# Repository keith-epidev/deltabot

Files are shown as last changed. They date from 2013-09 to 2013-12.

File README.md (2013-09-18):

Deltabot Project
================

This 'DeltaBot' is the product of Keith Brown's final year electronics project at [La Trobe University](http://www.latrobe.edu.au/). It falls under the umbrella project called [RepRap](http://reprap.org/). 

This repository serves as a place to store and track progress at a source level. Forcing software, hardware and designs into a single repository might not be the most practical use of git but it does allow me to easily share updates. Once the components come close to a stable release I will break this up into individual repos.

If you are interested, you can follow a brief blog at [http://printer.epidev.com](http://printer.epidev.com).

##Goals
- Cheap
- Modular
- CNC etching + 3D printing
- Produce alternative hardware, electonics and software. (Simply to learn)
- Automated Calibration

##Versions
There are three variants being produced by this project:  
1. Large robot  
2. Small, slow but strong platform  
3. Small, fast robot  

##Inspiration
Although I have not forked any current designs, this project is still based upon exiting work.
This project is primarily a derivative of the RepRap [Kossel](https://github.com/jcrocholl/kossel) by [jcrocholl](https://github.com/jcrocholl)
Of course I have also been inspired by other insane delta robots:
- [http://www.youtube.com/watch?v=Gv5B63HeF1E](http://www.youtube.com/watch?v=Gv5B63HeF1E)
- [http://www.youtube.com/watch?v=0-Kpv-ZOcKY](http://www.youtube.com/watch?v=0-Kpv-ZOcKY)
- [http://www.youtube.com/watch?v=NDzUiZsbQtw](http://www.youtube.com/watch?v=NDzUiZsbQtw)

And every other RepRap printer. But mostly The RepRap Project founder, Adrian Bowyer.
- [http://en.wikipedia.org/wiki/File:Adrian_Bowyer_-_PopTech_2007.webm](http://en.wikipedia.org/wiki/File:Adrian_Bowyer_-_PopTech_2007.webm)

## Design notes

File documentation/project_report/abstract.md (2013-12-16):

#(abstract.tex){
This document describes the design and development of an inexpensive 3D printer. The project is developed for the final year engineering project at La Trobe University by Keith Brown.

The printer will be in the form of a delta machine. The intention is to reduce the number of components and utilise cheaper hardware while still achieving a fast accurate print. The electronics will not be a direct derivative of current implementations. Experimentation with alternative architecture will be trialled with the goal of delivering a more computational capable system.

An introduction into 3D Printing and its concepts, advantages and issues is outlined. The commercial viability for both commercial and consumer markets is described. An analysis of both the structure and the systems inverse kinematic equations are included. Considerations regarding fluid motion is outlined. Hardware diagrams and descriptions follow. The electronic and software systems are discussed in detail. Testing procedures and associated results are also examined. Finally, project management tasks are reviewed.

}

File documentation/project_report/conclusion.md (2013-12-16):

Conclusion
==========

The macro and micro effects of an introduction to a personal manufacturing device is fascinating. It has the possibility to facilitate innovation in many areas. 
Whether it is a domestic or commercial application, 3D printing can help produce specialised parts, reduce prototyping time and cost, promote first hand recycling and entice the next generation into a technical field.

Low cost additive manufacturing is still in early development. A young underdeveloped device or idea presents an opportunity for improvement. This technology will continue to advance as demand increases. The delta style of 3D printers already is faster and more accurate then the traditional Cartesian machines.

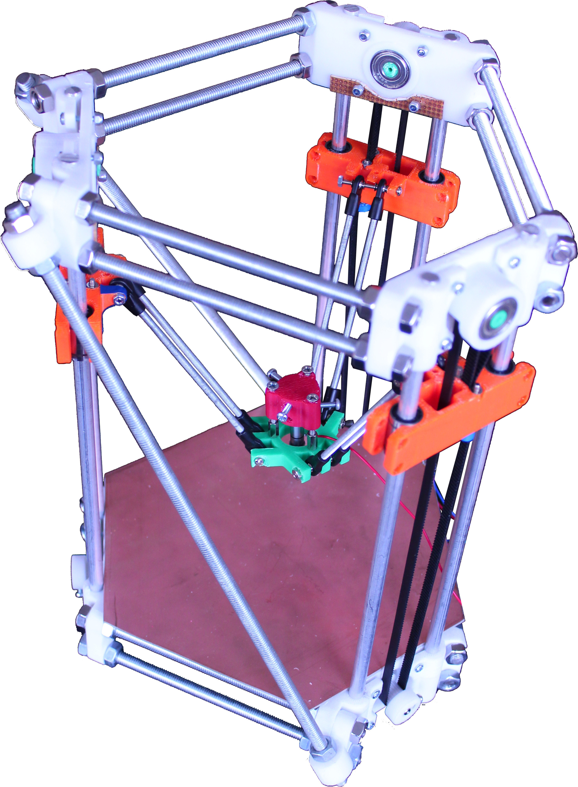
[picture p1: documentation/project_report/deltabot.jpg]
Final Deltabot Revision


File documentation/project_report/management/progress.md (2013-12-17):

Progress
========

A two complete frame has been designed and assembled. The first desktop model has a print area of roughly #10cm^3#. The second was a larger version using all the same printed parts but increasing the rod lengths. It is twice as tall and wide, resulting eight times the volume. This design has had small revisions made along the way and seems quite stable. The larger version does require a double cross strut for stability.

A plotter attachment was developed first for testing purposes. This has been used extensively. The extruder feed has also been prototyped although it has not been properly tested.

The second revision of electronics has been assembled and tested. While far better then the first revision, a third would add extra features and improve stability. No hardware mods are required for basic functionality.

The firmware has been developed during the entire development stage. Slowly improving and adding additional features. Currently it supports:
- Queuing of motion instructions
- Acceleration
- Console interface over UART
- LCD interface
- Homing and auto height calibration
- Command checksum validation

The complementary computer software is currently stable for 2D plots. It takes g-code generated from slic3r and converts it to motion descriptions for the printer. The communication side is capable of sending the instructions and validating that they were successfully received.

Shortcomings
-----------
For a complete working 3D printer the following tasks need to be completed:

- Develop extruder calculations for software
- Implement extruder feeder control
- Implement temperature PID loop
- Extend auto calibration
- Increase system clock to 20Mhz

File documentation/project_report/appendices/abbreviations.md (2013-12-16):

\chapter{Abbreviations}
\label{AppendixB}
\lhead{Appendix B. \emph{Abbreviations}}

| *ABS*  | *A*crylonitrile *b*utadiene *s*tyrene (plastic)                     |
| *AVR*  | *A*tmel's Alf (Egil Bogen) and *V*egard (Wollan)'s *R*ISC processor |
| *CAD*  | *C*omputer-*a*ided *d*esign                                         |
| *CPU*  | *C*entral *P*rocessing *U*nit                                       |
| *CRC*  | *C*yclic *R*edundancy *C*heck                                       |
| *FPU*  | *F*loating *P*oint *U*nit                                           |
| *MSP*  | *M*ixed *S*ignal *P*rocessor                                        |
| *LCD*  | *L*iquid *C*rystal *D*isplay                                        |
| *PLA*  | *P*oly*l*actic *a*cid (plasic)                                      |
| *SPI*  | *S*erial *P*eripheral *I*nterface                                   |
| *SVG*  | *S*calable *V*ector *G*raphics                                      |
| *UART* | *U*niversal *A*synchronous *R*eciever/*T*ransmitter                 |
| *USB*  | *U*niversal *S*erial *B*us                                          |
	List of abbreviations

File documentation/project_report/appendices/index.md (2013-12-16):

#(appendices.tex){

![documentation.md]
![abbreviations.md]
![schematics]
![layout]
![code.md]
![cad.md]

}

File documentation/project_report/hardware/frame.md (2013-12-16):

Frame
=====

The first iteration of design utilised aluminium to build the framework. It was selected due its strength and the modularity it offered during the prototyping stage.

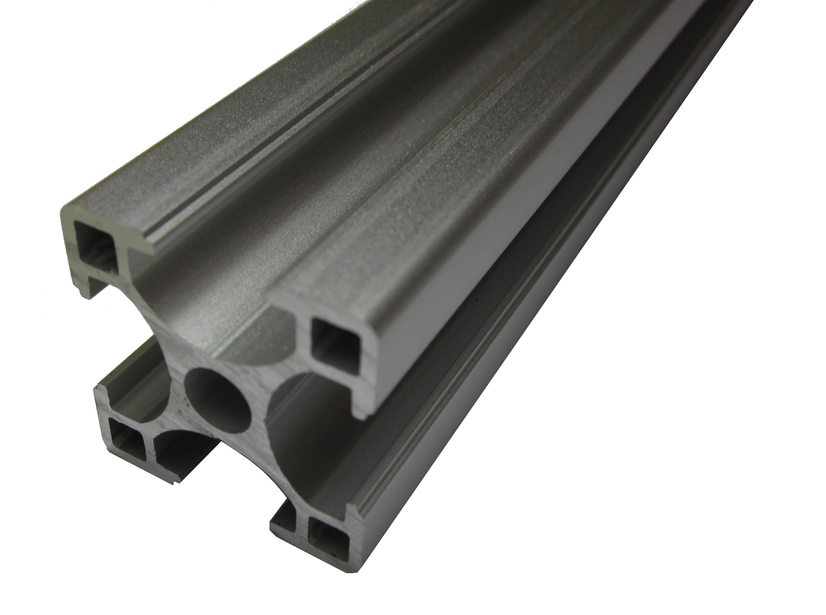
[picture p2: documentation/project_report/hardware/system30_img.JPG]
System30 Beam


Positives
- Very strong in any direction
- Simple mounting and joining
- Reusable
- Easy to modify / tune

Negatives
- Relatively expensive at $25 per meter
- Requires special cutting tools
- Hard to source

However during the initial design, it was decided that the carriage designs would be too complex which would violate one of our design goals. The very cheap and easily obtained 8mm threaded and smooth rods were used instead. This way we can use LM8UU linear bearings instead of investing a lot of time in hardware design.

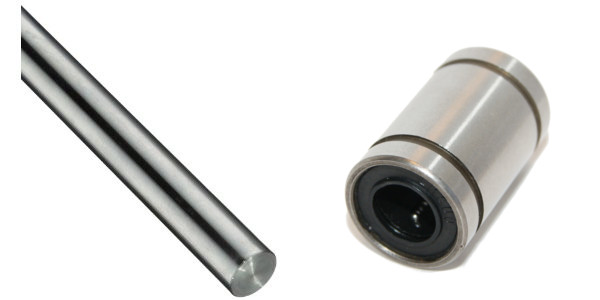
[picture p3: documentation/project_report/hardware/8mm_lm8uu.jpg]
8mm round bar and LM8UU Linear bearings

Positives
- $3.3 per meter for stainless steel round bar
- $0.90 per meter for 8mm threaded rod.
- $0.75 per unit for LM8UU linear bearings.
- Easy to obtain from metal fabricators or general hardware stores
- Can cut with a hacksaw or angle grinder

Negatives
- Flexes in the horizontal direction

Early Sktech Of Frame Design

The frame will have a small enclosed area for the electronics and power supply. The printer bed is mounted on top of the case. There is a beam on the top level that intersects the face in half. This is primarily for a place to mount the plastic feeder but also serves as a structural support beam.

We will need to know how much material to order. There is 4 equilateral triangles with side lengths of #D#  and there are 4 rails that need to be of #D#. 
##M_{threaded} = 3(4D) + 2(D\sqrt{3}) ##
##M_{smooth} = 3(2*2D)  ##
To minimise waste, #D# needs to be a multiple of the purchased material's length.  To further reduce waste, the purchased length should be close to a whole number.

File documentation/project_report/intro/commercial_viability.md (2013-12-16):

Commercial Viability
====================

This old technology is becoming established in a new market. While it becomes more accessible, new opportunities begin to emerge and intern, increases demand. Prices are decreasing, materials are becoming more accessible and there is an increasing amount of printable designs being uploaded to the Internet. The later attributes the most positive influence to the 3D printing market. This makes an old product more valuable.

Growth of CAD designs on thingiverse.com cite[6]

It is clear that this market is expanding at a promising rate. Furthermore because there is such a diverse range of neighbouring markets that will benefit from this technology, it is likely that it will be supported by commercial demand alone. Applications for 3D printing have yet to be completely discovered, the boundaries are always being pushed by innovators. It is apparent that a very successful industry has been created.

Commercial Market
-----------------

3D printing can help many different businesses. For example; Product designers can produce prototypes within a few hours, prosthetics can be made for a person more frequently and engineers can produce custom parts easily. It is important to note that even if a 3D printer existed in every home, there are still many skills that can't be replaced by automation. Downloading a generalised product will never replace a professionally crafted custom version. 3D printing just streamlines the development cycle and promotes rapid growth.

Rapid prototyping reduces development costs and creates new opportunities. It is possible that we will see a rise in hardware start-ups similar to the influx of software start-ups we have seen recently. It may be more feasible for a young company to attempt entering into established markets with little overhead.

Consumer Market
---------------

There is a number of reasons why an individual might desire a 3D printer. It may help reduce our consumption rate by allowing us to easily repair broken household items. While it is unlikely for the average person to need a miniature factory, it is ideal for hackers, hobbyists, artists and craftsmen

Currently, the largest consumer market for 3D printing falls inside the open source community. Although intellectual property is freely shared, support and labour is very valuable. These customers are generally open to early adoption of new technology. The network of passionate, diversely skilled customers strive to improve the current designs and collaboratively innovate the CNC scene.

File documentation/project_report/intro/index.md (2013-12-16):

Introduction
============

3D Printers have received a lot of media attention recently. Additive manufacturing has been around for at least 30 years cite[1, 2]. However, in the last five years popularity has increased dramatically due to the availability of much cheaper entry level machines. It is now possible for the general public to purchase pre-assembled printers at a similar cost as a personal computer.

There will always be innovation and dangers associated with a new technology. We already have prime examples of both aspects; At a 2011 TED talk, Dr Anthony Atala presented a human kidney prototype that his team had printed cite[3]. Late 2012 Cody Wilson uploaded a video to Youtube that showed himself firing a gun mostly composed of 3D printed parts cite[4].

The environment will benefit from this new way of producing products. Firstly, plastic items can be recycled and reused to create new, more useful items. This not only reduces costs but it also eliminates transportation of new items. They no longer need to be imported and transported all over the country, they can just be downloaded.

Whilst companies like Objet and Stratasys produce printers for the commercial sector, it is hobbyist style printers that have spread awareness of such technology. The Reprap foundation has produced numerous models under the GPL licence. Their main goal is to produce an affordable device that can self replicate. All of the designs are available to download and print. Makerbot Industries is a comercial operation that was born from an open source community.

Online services such as Shapeways provides 3D printing services. This allows their customers to receive a higher quality print without investing in expensive hardware. CAD design community sites have also been very popular such as 'thingiverse.com'. There are over 30,000 free designs including a key-chain fob, mobile phone case, model radial engine and even 3D printer parts and upgrades.

![printing_methods.md]
![fdm_articulation_implementations.md]
![fdm_accuracy_materials.md]
![proposed_solution.md]
![commercial_viability.md]

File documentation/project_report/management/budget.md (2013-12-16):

Budget
======

There are many consumer 3D printers on the market currently. They range from $450 to over $20,000. One of the primary goals of this project is to produce inexpensive electronics to help reduce the overall cost of 3D printing. $450 is very competitive if the quality is reasonable. The final target cost for this project is a base model for $350 AUD. I have considered many aspects that will help minimise costs:

- low end 8bit AVR ATmega value line microcontrollers
- Single board solution
- Optional components: Flash memory, LCD and Ethernet.
- Minimal hardware
- Printed gears for belt drive
- Balance of cost vs quality for stepper motors
- Use common hardware store smooth and threaded rods

Revenue
-------
La Trobe University kindly provides a $200 spending budget for final year projects. I will personally fund the remaining fees.

Expenses
--------
Most parts were able to be recycled through each design iteration.

| Item                     | Cost |
|──────────────────────────|──────|
|──────────────────────────|──────|
| 6 meters of smooth rod   | $20  |
| 6 meters of threaded rod | $6   |
| PCB Fabrication          | $40  |
| Electronic components    | $70  |
| 4 Stepper motors         | $60  |
| 1kg ABS Plastic          | $30  |
| Assembled Extruder       | $50  |
| Power supply             | $30  |
| Heated Bed               | $50  |
| 4 metes of Belts         | $16  |
| 6 608zz Bearings         | $6   |
| 6 LM8UU Bearings         | $8   |
| Assorted hardware        | $50  |
|──────────────────────────|──────|
| Total                    | $436 |
|──────────────────────────|──────|
	Budget allocation

Non-budgeted resources
----------------------

| Item                                                                       | Provided By                           |
|────────────────────────────────────────────────────────────────────────────|───────────────────────────────────────|
|────────────────────────────────────────────────────────────────────────────|───────────────────────────────────────|
| Atmel AVR Dragon JTAG programmer                                           | Robert Ross                           |
| Host computer and development software                                     | Keith Brown                           |
| Soldering equipment                                                        | Department of Electronics Engineering |
| CRO and testing equipment                                                  | Department of Electronics Engineering |
| Breadboard, Pliers, cutters, Multimeter and other general electronic items | Keith Brown                           |
|────────────────────────────────────────────────────────────────────────────|───────────────────────────────────────|
	Non-budgeted resources

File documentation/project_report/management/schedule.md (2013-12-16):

Schedule
========

The original schedule had to be modified in order to accommodate the extra unplanned revisions for both hardware and electronics. From May up until late October, three design iterations of hardware were developed. Each time improving on a major design flaw. Each iteration had a large impact on the schedule, however all were necessary hurdles that contributed to the final product. A second revision of electronics was required after the project goals were re-evaluated and to remove a few bugs.

The additional time added to the timeline pushed some of the key functionality past important dates such as the final presentation. Work has continued after the main delivery dates and a fully functioning 3D printer is estimated to be achieved at the end of January 2014.

An online project log was kept. Posts were made at regular intervals, discussing progress and small milestones. This served as a great resource and helped keep track of ongoing progress. It is available at [http://printer.epidev.com](http://printer.epidev.com).

![gantt.tex]

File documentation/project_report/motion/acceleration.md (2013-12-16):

Acceleration
============

Acceleration is required to ensure smooth motion is maintained. Smooth motion is essential for reaching high speeds and also to minimise a stepper motor skipping a step. The rate of acceleration can be written as a function of current and next frames momentum.  We are only concerned with the momentum of the actuator carriages, not the momentum of the platform.

## P = mv ##
where #P# is momentum,
#m# is mass,
#v# is velocity.
So to decrease momentum around sharp bends, we must reduce the speed of the actuator.

Once the system has been constructed, we will need to run tests to work out the maximum speed that we should attempt to accelerate to. Jerk is the derivative of acceleration. It can be thought of as how fast can we accelerate? This also will need to be thoroughly tested. But we can write it as a variable so that we can later substitute different values.

The acceleration algorithm is as follows:

- calculate the closest change in direction for any actuator
- if change is less then 100 steps decrease speed by A
- if change is greater then 100 increase speed by A
- if maximum speed has been reached do nothing.
- repeat next step

This creates a smooth linear acceleration. We could also implement more detailed patterns that perhaps use a quadratic to reach the maximum speed sooner.

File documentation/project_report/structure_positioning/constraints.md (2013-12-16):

Constraints
===========

Printing Bed
------------
A design assumption was made at the beginning of this section; The platform can not be positioned outside of the frame. To force this rule to apply, we must set the linkages length equal to the minimum distance from a rail to a side of the frame. The maximum length required is a line straight down the y axis from the rail to the frame which is equal to #{\sqrt{3}\over 2}D#. If we swing the platform around, pushing it to the maximum radius that this length permits, we see that the path is not actually a circle but a rounded triangle. The light blue path in fig. ref[top-view-angle_diagram.svg] is the maximum positions. Such an unusual path is typically not needed, so we will simplify our problem by using a circular print bed.

To allow for a platform, we must subtract its radius from each of the linkages length. So, our rule for #h# is:
##h = {\sqrt{3}\over 2}D - r ##

Universal Joint Angle Range
---------------------------

Universal joint angle horizontal range

The universal joints that will pivot to allow full movement will need to be capable of a certain range. This can be calculated exactly with:

## \theta = 60 - 2 \arctan{({  { {2 - \sqrt 3 }\over 2} r  \over  {1\over 2} D   } )} ##

Practically, we can simplify the problem by aiming for #60^{\circ}# in the horizontal direction and #90^{\circ}# in the vertical direction.

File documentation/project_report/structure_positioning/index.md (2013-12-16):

Structure and Inverse Kinematics 
================================

The hardware design will be in the form of a delta machine. These devices can perform fast accurate tasks as the light-weight print head is capable of quick acceleration. This design has been adopted from a current reprap project cite[5]. The delta machine will use less parts then a traditional Cartesian machine.

For a detailed overview of this projects design please refer to the Design Document

![structure.md]
![one_dimension.md]
![platform.md]
![vertical_travel.md]
![two_dimension_vert.md]
![two_dimension_horz.md]
![platform_horz.md]
![three_dimension.md]
![constraints.md]

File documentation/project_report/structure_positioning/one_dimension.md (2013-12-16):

Simple one dimension position
===========================

Lets consider one dimension to begin with, Figure 1 illustrates the movement of three key points; the platform and the left and right linear actuators. We can see that if the linkages are the same length as the vertical distance, the platform is capable of reaching any position along the #x# axis.

//[Simple ideal motion](svg:1)

Also, it can be seen that a vertical actuator requires an equal amount of travel to permit full movement. It is important to note that the platform is considered a point source in this example. Practically this is not the case as we will require a place to mount tools.

For a desired position of #p(x)#, we need to derive where to place linear actuators. Take fig. ref[structure_simple.svg] below, lets derive the equations that will translate a desired #x# into #a_1# and #a_2#. 

Simple one dimension parameters

Firstly, lets derive relationship between #x# and #a_1#:
## (1)\  h^2 = a^{2}_{1} + b^{2}_{1} ##
##  \Leftrightarrow  a_{1} = \sqrt{ h^2 - b^{2}_{1} }##
## (2)\  b_1 = x - (-D)##
## \Leftrightarrow\  b_1 = x + D##
substituting (1) into (2) gives
## a_1(x) = \sqrt{ h^2 - ( x + D )^2 }##
Now, lets find the relationship between #x# and #a_2#:
## (3)\  h^2 = a^{2}_{2} + b^{2}_{2}##
##  \Leftrightarrow  a_{2} = \sqrt{ h^2 - b^{2}_{2} }##
## (4)\  b_2 = x - D##
finally, substituting (4) into (3)
## a_2(x) = \sqrt{ h^2 - (x - D)^2 } ##

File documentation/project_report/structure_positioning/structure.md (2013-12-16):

Structure
=========

A delta machine consists of a number of kinetic chains that meet at a central platform. This platform can be moved by actuating the pivots connected to the main structure. The platform is kept parallel to the floor during motion. Figure ref[structure_diagram.svg] represents a simple two armed delta machine. The two-dimensional diagram helps to illustrate the important lengths and vectors. After we have analysed a two dimensional machine we will apply these concepts to three-dimensions.

Structure Diagram

| #D# | Distance from actuator to origin                       |
| #L# | Vertical length of the frame                           |
| #a# | Height of the actuator pivot point from the origin     |
| #h# | Length of the kinetic linkage                          |
| #r# | Radius of the platform                                 |
| #p# | Position of the extruder tip or centre of the platform |
| #O# | Origin of the system                                   |
| #x# | Horizontal vector                                      |
| #y# | Vertical vector                                        |
| #z# | Depth vector                                           |
|─────|────────────────────────────────────────────────────────|
	List of vectors

The following assumptions are made to help define the system:
- Platform and linkages must stay within the frame's outer rails.
- Linkages are not restricted in any way, they may swivel on their joins in any direction.
- The platform can not move down past the base.
- Linkages are restricted to the rail's length.
- Linkages can not stretch or contract.

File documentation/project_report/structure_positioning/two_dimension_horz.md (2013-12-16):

Two dimensional position in the horizontal plane
==============================================

Now its time to examine how adding a third actuator allows for two dimensional movement in the horizontal plane. Figure ref[top-view_diagram.svg] is a top-down view of our system. The actuators are placed in a equilateral triangle formation to distribute the load evenly. The position of the platform can be altered by changing the lengths of the linkages horizontal component, the #b# term. Remember, this is not stretching the linkages, it is merely displacing length between the horizontal and vertical component - the hypotenuse remains the same. By looking straight down into the system, only the #b# vectors are visible, the carriages on the rails or the #a# term is  directed in/out of the page.

The coordinates system has been aligned with the actuators to help simplify the problem. The origin is placed at the centre of the print bed. Please note that the print bed is represented as a circle with its radius equal to the minimum distance from the origin to the frame. 

To control the platforms position we must modify the carriages vertical position #a#. However, the horizontal plane position is completely dependent on #b#. We have already established the relationship between #a# and #b#, and that is #a = \sqrt{ h^2 - b^2}#. We now need to develop the relationship between #b# and the position (#x,y)#.

Each actuator will have its own equation for calculating its #b# term. This is because they are not placed uniformly around the coordinates system even though they are equally apart. Firstly, the general rule for calculating #b# as a function of the platforms position:
##b_n(x,y) = |\overrightarrow{R_n P(x,y)}|## Where R is the position vector of the target actuator and P is the position vector of the platform.

Top view components

Figure ref[top-view_diagram.svg] illustrates that this problem can be solved by a simple application of Pythagoras' theorem again.

Top actuator:
##d_1(x) =  x##
##e_1(y) =  y - D##
##b_1(x,y) = \sqrt{d_1^2 + e_1^2}##
##b_1(x,y) = \sqrt{ x^2 + (y - D )^2}##
Bottom left actuator:
##d_2(x) = x - (-d\sqrt{3}/2)##
##e_2(y) = y - (-d/2)##
##b_2(x,y) = \sqrt{ ( x + {d\sqrt(3)\over 2})^2 + ( y + {d\over 2})^2   } ##
Bottom right actuator:
##d_3(x) = x - D\sqrt{3}/2##
##e_3(y) = y - (-D/2)##
##b_3(x,y) = \sqrt{ ( x - {D\sqrt(3)\over 2})^2 + ( y + {D\over 2})^2   } ##

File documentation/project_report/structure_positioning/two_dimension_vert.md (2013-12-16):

Two dimensional position in the vertical plane
============================================

Now we are able to examine how we may add a vertical component to the system. From the last sections we discovered that the length required for the vertical actuators is the equal the linkages length. In this example, we have created a square printable area of #(2D)^2#. This is possible as the rails are twice the length of the linkages length or #L = 2(2D)#. 

//[Two dimensional motion](svg.4)

Introducing the #z# component directly adds to the #a_1# and #a_2# terms. The position equations are amended as:

## a_1(x) = \sqrt{ h^2 - (x + D - r)^2 } \color{red}{ + z}##
## a_2(x) = \sqrt{ h^2 - (x - D + r)^2 } \color{red}{ + z}##

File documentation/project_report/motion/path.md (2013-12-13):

Path Tracing
============

Once a three dimensional object has been split up into two dimensional layers, the extruder head must trace the outlines of each layer. Once a layer has been traced, the z component moves a step down and the extruder will trace the next layer. The process repeats until all layers have been extruded leaving a fully formed three dimensional object.

To move the extruder in a desired direction, we must calculate the distance and direction that each actuator must travel. This can be done by subtracting actuator heights from the last position with the heights of the next move. This gives us three vectors describing the distance and direction. The next step is to translate these distances into corresponding speeds. To move in a straight line, each actuator must complete their respective distances at the same time. 

So to calculate how fast each actuator must move, we first start with:

## speed = displacement / \Delta time ##

So we can see that keeping the time constant for all three actuators, only displacement affects speed. Actually speed is directly proportional to the distance that needs to be travelled. 

But how long is an acceptable time to travel? This is quite simple once the maximum speed is determined. The actuator with the largest displacement should travel at maximum speed.

## \Delta time = displacement / MAX(speed) ##

Now we simply substitute the same #\Delta time# for the other actuators. Now we have proportional motion!

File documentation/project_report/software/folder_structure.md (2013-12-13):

Folder Structure 
================

I have chosen to set the firmware directory in a way that attempt to separate non similar objects. For example system settings should not be located in the same directory as code for a LCD.

The following list illustrates the basic structure:

- *dev* contains sub folders that have code relating to physical components such as LCD and stepper motors
- *etc* contains configuration files such as clock speed, pin descriptions and macros
- *lib* contains reusable software objects such as buffers
- *main* holds different top level files (useful for different applications or tests)
- *sys* has anything to do with the microcontroller architecture

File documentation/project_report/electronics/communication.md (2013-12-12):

Communication
=============

An FTDI FT220X USB to UART converter is used for communication between the host computer and the printer. It runs at a baud rate of 38400, however burst commands can be sent due the internal FILO buffer included in the integrated circuit. A micro USB header was selected so that common android phone cables can be used.

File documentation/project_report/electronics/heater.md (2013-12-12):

Heating elements
================

A powerful MOSFET is used to push large current through a small resistor. This produces heat. The heat can be monitored with a robust thermistor. A PID loop will smoothly and accurately maintain a specific temperature. Two heat ports are available; one for the extruder and one a heated bed.

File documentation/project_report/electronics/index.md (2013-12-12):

Electronic Systems
==================

![methodology.md]
![top_level.md]
![microcontroller.md]
![motor_drivers.md]
![communication.md]
![heater.md]
![sensors.md]
![power.md]
![safety.md]

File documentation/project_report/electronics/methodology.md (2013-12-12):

Methodology
==========

The first iteration of electronics were designed around the goal of modularity. While it offered the needed flexibility during the prototyping stage, a few shortcomings forced a redesign. It featured small daughter boards that vertically plugged into a mainboard. Exposing a SPI bus as ports that could accept any type of add on provides a possible upgrade path in the event of a necessary addition. 

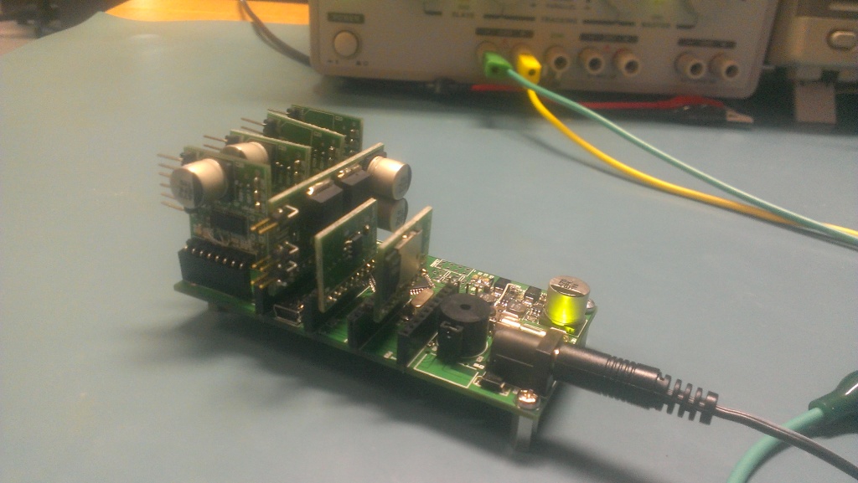
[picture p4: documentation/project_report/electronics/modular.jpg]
First iteration of electronics


Unfortunately this configuration was too flimsy. Stepper drivers were damaged during testing. There is a lot of manual work required to assemble such a design and would not be practical for a final product.

The second revision was designed to be a simple low-cost single board solution. Instead of being a complete standalone product, this version is designed to leverage of a host computer. No external memory is used so a computer must constantly feed G-Code commands during a print. 

Second revision

One of the main goals of revision two was to be cross compatible with the exiting community firmware. The most compatible firmware is ['Teacup'](http://github.com/Traumflug/Teacup_Firmware) . Furthermore, any software that I develop should be cross compatible with existing hardware such as RAMPS.

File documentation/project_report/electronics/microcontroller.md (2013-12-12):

Microcontroller
===============

The Microcontroller that has been selected is an Atmel 8-bit ATmega644. It was selected due to its low cost, small footprint and compatibility with existing firmware. The large ATmega family also allows for an upgrade path if required. It can be clocked up to 20MHz however I am using 10AU model which has a maximum of 10Mhz. The 10AU is available in single quantities at $4 compared to the 20Mhz at $11.

The package includes 64 Kbytes of flash memory. It has 44 pins with a total of 32 GPIO available. No USB communication is integrated so a USB to UART chip is required. The physical package selected was a TQFP so that it can be easily soldered with a standard soldering iron.

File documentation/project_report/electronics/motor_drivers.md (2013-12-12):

Motor Drivers
=============

TI DRV8825 integrated motor drivers were selected to drive the stepper motors. They can be configured to drive a single bipolar stepper motor at 2.5A with up to 1/32 microstepping. They do not require many external passive components. They feature a useful error signal pin that goes high in the event of over current or heating issues. A heat sink should provide adequate heat dissipation.

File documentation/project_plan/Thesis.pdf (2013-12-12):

LA TROBE UNIVERSITY (http://www.latrobe.edu.au)

# Delta Printer Project Plan

by

## Keith Brown

Final Year Project Report

in the
Faculty of Science, Technology and Engineering (http://www.latrobe.edu.au/scitecheng/) Department of Electronic Engineering (http://www.latrobe.edu.au/ee)

## December 2013

# Declaration of Authorship

La Trobe University | Department of Electronic Engineering

## Statement of Authorship INDIVIDUAL SUBMISSION

Please read the following instructions and associated University documents before completing and submitting this form with your item of assessment.
1. A Statement of Authorship must be completed for all items of assessment where the assessment is worth ten percent (10%) or more of the total for the unit.
2. The Academic Misconduct Policy found at http://www.latrobe.edu.au/policies
3. Statute 16 found at http://www.latrobe.edu.au/legalservices/statutes.html
4. Regulation 16.2 found at http://www.latrobe.edu.au/legalservices/regulations.html

I certify that the attached material is my original work. I declare that no other person's work has been used without due acknowledgement. Except where I have clearly stated that I have used some of this material elsewhere, it has not been presented by me for examination in any other course or unit at this or any other institution.
I have read the Academic Misconduct Policy, Statute 16 and Regulation 16.2 relating to Student Discipline and Academic Misconduct, which are available on the University's web site and understand that I am bound by such Policy, Statute and Regulation and that I may be subject to student discipline processes in the event of an act of plagiarism by me.
I understand the nature of plagiarism to include the reproduction of someone else's words, ideas or findings and presenting them as my own without proper acknowledgement. Further, I understand that there are many forms of plagiarism which include direct copying or paraphrasing from someone else's published work (either electronic or hard copy) without acknowledging the source; using facts, information and ideas derived from a source without acknowledgement; producing assignments (required to be independent) in collaboration with and/or using the work of other people; and assisting another person to commit an act of plagiarism.
I understand that the work submitted may be reproduced and/or communicated by the University or a third party authorised by the University for the purpose of detecting plagiarism.
I agree for the Department to keep a copy of my assignment for a database.
Unit Code: |
Unit Name: |
Lecturer/Tutor's name : |
Name of Document: |
Student Number: |
Family Name: |
Given Names: |
Signature of Student: |
Date Submitted: |

i

LA TROBE UNIVERSITY (http://www.latrobe.edu.au)

# Abstract

Faculty of Science, Technology and Engineering (http://www.latrobe.edu.au/scitecheng/)

Department of Electronic Engineering (http://www.latrobe.edu.au/ee)

Bachelor of Electronic Engineering

by Keith Brown

This document describes the project plan for an inexpensive 3D printer. The project is

developed for the final year engineering project at La Trobe University by Keith Brown.

The printer will be in the form of a delta machine. The intention is to reduce the number

of components and utilise cheaper hardware while still achieving a fast accurate print.

The electronics will not be a direct derivative of current implementations. Experimen-

tation with alternative architecture will be trialled with the goal of delivering a more

computational capable system.

An introduction into 3D Printing and its concepts, advantages and issues is outlined.

The commercial viability for both commercial and consumer markets is described. This

projects primary, secondary and tertiary objectives are listed. The strategies to achieve

these goals is also described, followed by budget requirements and lastly a detailed

schedule is included.

# Acknowledgements

I would like to share my sincere gratitude to Professor Robert Ross, my primary su-

pervisor whom has given me so much creative control. Robert has provided constant

assistance. He also has bestowed me with his precious technical expertise. Adam Con-

sole my co-supervisor, has helped steer this project in the right direction on numerous

occasions. It was Adam that suggested the delta machine design. His diverse knowledge

is irreplaceable.

The RepRap community has paved the way for projects like this. There is a wealth of

freely available information on their website and forums. I hope that I will be able to

express my appreciation by giving something back to the open source community.

I would like to personally thank everyone who has supported me. I have discussed this

project with many of my friends and family, who have contributed with valuable support

and feedback.

iii

# Contents

Declaration of Authorship | i
Abstract | ii
Acknowledgements | iii
List of Figures | v
List of Tables | vi
1 Introduction | 1
2 Project Objectives | 7
3 Objective Strategy | 9
4 Project Management | 14

iv

Contents | v
5 Conclusion | 18

# List of Figures

1.1 Growth of CAD designs on thingiverse.com | | 5
3.1 Frame Design | | 9
3.2 System block diagram | 10
3.3 Agile Development Process | 12
4.1 Gantt Chart | 15

vi

# List of Tables

3.1 List of possible risks | 13
3.2 List of actions | 13
4.1 List of important dates | 14
4.2 Budget allocation | 17
4.3 Non-budgeted resources | 17

vii

# Chapter 1

# Introduction

3D Printers have received a lot of media attention recently. Additive manufacturing has

been around for at least 30 years<cite>1, 2</cite>. However, in the last five years

popularity has increased dramatically due to the availability of much cheaper entry level

machines. It is now possible for the general public to purchase pre-assembled printers

at a similar cost as a personal computer.

There will always be innovation and dangers associated with a new technology. We

already have prime examples of both aspects; At a 2011 TED talk, Dr Anthony Atala

presented a human kidney prototype that his team had printed<cite>3</cite>. Late

2012 Cody Wilson uploaded a video to Youtube that showed himself firing a gun mostly

composed of 3D printed parts<cite>4</cite>.

The environment will benefit from this new way of producing products. Firstly, plastic

items can be recycled and reused to create new, more useful items. This not only

reduces costs but it also eliminates transportation of new items. They no longer need

to be imported and transported all over the country, they can just be downloaded.

Whilst companies like Objet and Stratasys produce printers for the commercial sector,

it is hobbyist style printers that have spread awareness of such technology. The Reprap

foundation has produced numerous models under the GPL licence. Their main goal is

to produce an affordable device that can self replicate. All of the designs are available to

download and print. Makerbot Industries is a comercial operation that was born from

an open source community.

Online services such as Shapeways provides 3D printing services. This allows their

customers to receive a higher quality print without investing in expensive hardware.

CAD design community sites have also been very popular such as ’thingiverse.com’.

1

Introduction | 2

There are over 30,000 free designs including a key-chain fob, mobile phone case, model

radial engine and even 3D printer parts and upgrades.

## 1.1 3D printing methods

Additive manufacturing is the process of constructing a three-dimensional object by

depositing material in discrete layers. Conversely, traditional machining methods are

subtractive; material is removed to expose the desired object. This printer utilises an

additive method as it produces fine plastic layers to build an object. There are many

different approaches of additive manufacturing. The main four methods are outlined in

the following paragraphs.

Fused deposition modelling or FDM is the method of extruding thermoplastics in layers.

This project is considered to use an FDM method as it extrudes fine plastic layers to build

an object. The printer deposits plastic material by melting it through a hot extruder.

The extruder resembles a metal funnel that takes solid plastic and produces liquid plastic

out of a small hole. The liquid plastic can be fused to previously deposited material. The

machine must physically move the extruder around an area, while placing plastic where

it is required. This process is repeated layer by layer to achieve a three-dimensional

object. The technology was invented by S. Scott in 1980 <cite>2</cite>.

Selective laser sintering or SLS is a technique that allows either metal, plastic, ceramic

and glass powder to be fused together with a powerful laser. The laser targets cross-

sections, selectively fusing a fine layer of powder to the object. Once a layer has been

complete, a fresh layer of powder is dusted over the object and the process repeats.

The left over material acts as a support for the object being manufactured. After the

procedure has finished, the excess powder can be removed and used for the next print.

The process is slow, producing porous but strong results.

Stereolithography or SLA is the method of using an ultraviolet light to cure a photopoly-

mer. The printing platform sits in a vat of liquid resin. The light targets a cross-section

of the desired object and the exposed resin will solidify. Once the layer has completed,

the platform will move down allowing for another layer to be added to the model. SLA

produces accurate results but is a very slow process. SLA has received a lot of attention

recently as the method has been adopted by a handful of young start ups. It offers a

much greater result compared to the current generation of FDM printers. However the

hardware and resin is very expensive.

Laminated object manufacturing or LOM is another rapid prototyping method. It uses

a laser or a knife to cut out layers from an adhesive-coated material. The layer is

Introduction | 3

then heated and pressed onto the previous layers. A new sheet of material is rolled in

place and the process repeats. This method can be relatively cheap as readily available

material such as paper can be used.

Each process is managed by a technique called ’computer numerical control’ or CNC.

This method is essentially computer controlled automation. Three-dimensional models

are developed using ’Computer aided design’ or CAD. These CAD models are processed

to produce CNC commands known as G-code. The G-codes are instructions that tell

the machine how to produce the CAD model.

## 1.2 FDM Articulation implementations

A Cartesian Gantry structure is the most common implementation. It consists of a

linear actuator for each axis of freedom. The horizontal plane generally has a sturdy rail

that a bridge is mounted on, this rail permits motion in the x direction. A carriage is

mounted to a rail that connects the bridge together. The carriage can move along this

rail and therefore permits motion in the y direction. Lastly the carriage has a tool that

is capable of actuating in and out in the z direction.

The Gantry system is a well tested framework and is industry standard. It can be

found in many applications from small desktop CNC machines to huge container cranes.

While the frame is very strong, each linear actuator is dependent on another. The bridge

actuator has to be the strongest as it must provide enough force to move the bridge,

carriage and tool. This becomes an issue for fast moving applications as the momentum

will be relatively large.

The Delta robot has three vertical rails placed in the formation of an equilateral triangle.

Each linear actuator moves in the same direction and has kinetic linkages that connect

each carriage to a central platform. This platform can be positioned by placing each

carriage at a certain height. This is an improvement over the Gantry setup because each

actuator shares the load equally. It is capable of faster speeds because there is less load

on the tool end.

## 1.3 FDM accuracy and materials

Currently, leading consumer 3D printers can produce objects with layers heights of 0.1

millimetres. Such an accurate print will generally take around five hours for a medium

sized print. Pricing for a mostly pre-assembled unit is around USD$2,200.

Introduction | 4

Currently there are two main types of plastics readily available for FDM printing. Firstly

Acrylonitrile Butadiene Styrene or ABS is a strong material. It is a oil based plastic that can be melted and extruded at a temperature of approximately 105°C. It is fairly

cheap at $40 a Kg. It does contract slightly as it cools.

Polylactic Acid or PLA is another alternative that can be used for FDM printing. It

is marginally less expensive then ABS. While being more brittle then ABS it does not

contract as much. PLA is a biodegradable polymer and actually is produced by corn

starch. Because of it’s lower melting point it is not ideal for applications related to heat.

## 1.4 Proposed Solution

The delta machine design has been adopted for this project. Recently the Rostock

project has spawned many derivatives, most achieving cheaper construction over the

last generation of reprap printers. Delta machines have been used for many applications

including; pick and placers, packaging and production line sorters.

Its simplicity helps reduce hardware costs. But the biggest advantage is the machines

speed and accuracy. If the central platform is kept light, fast acceleration can be main-

tained. This permits the machine to perform in a sporadic manner while maintaining

an accurate position.

The electronics system will not be a derivative of current implementations. I will ex-

periment with different architectures with the goal of producing a much cheaper but

fully capable system. The components will be made modular to allow for a high level of

customisation. This helps to keep the main-board costs low but still permits additional

more expensive upgrades such as a Ethernet add on.

## 1.5 Commercial Viability

This old technology is becoming established in a new market. While it becomes more

accessible, new opportunities begin to emerge and intern, increases demand. Prices are

decreasing, materials are becoming more accessible and there is an increasing amount of

printable designs being uploaded to the Internet. The later attributes the most positive

influence to the 3D printing market. This makes an old product more valuable.

Introduction | 5

●●●●●●●●●●●●●●●●●●●●●●●●●●●

●●●●

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
2009 | 2010 | 2011 | 2012 | 2013

0 5000 10000 15000 20000 25000 30000

## Growth of items uploaded to Thingiverse

Time (years)

Number of new items uploaded

Figure 1.1: Growth of CAD designs on thingiverse.com

It is clear that this market is expanding at a promising rate. Furthermore because there

is such a diverse range of neighbouring markets that will benefit from this technology,

it is likely that it will be supported by commercial demand alone. Applications for 3D

printing have yet to be completely discovered, the boundaries are always being pushed

by innovators. It is apparent that a very successful industry has been created.

### 1.5.1 Commercial Market

3D printing can help many different businesses. For example; Product designers can

produce prototypes within a few hours, prosthetics can be made for a person more fre-

quently and engineers can produce custom parts easily. It is important to note that

even if a 3D printer existed in every home, there are still many skills that can’t be

replaced by automation. Downloading a generalised product will never replace a profes-

sionally crafted custom version. 3D printing just streamlines the development cycle and

promotes rapid growth.

Introduction | 6

Rapid prototyping reduces development costs and creates new opportunities. It is possi-

ble that we will see a rise in hardware start-ups similar to the influx of software start-ups

we have seen recently. It may be more feasible for a young company to attempt entering

into established markets with little overhead.

### 1.5.2 Consumer Market

There is a number of reasons why an individual might desire a 3D printer. It may help

reduce our consumption rate by allowing us to easily repair broken household items.

While it is unlikely for the average person to need a miniature factory, it is ideal for

hackers, hobbyists, artists and craftsmen

Currently, the largest consumer market for 3D printing falls inside the open source

community. Although intellectual property is freely shared, support and labour is very

valuable. These customers are generally open to early adoption of new technology. The

network of passionate, diversely skilled customers strive to improve the current designs

and collaboratively innovate the CNC scene.

# Chapter 2

# Project Objectives

There are many components required to complete this project. To have a functioning

3D printer, it is essential that all primary objectives are completed. Secondary Objec-

tives may be attempted if the primary goals have been satisfied before the development

deadline. These potential tasks would greatly improve the final product. Finally, the

tertiary objectives are considered not in the current project scope due to budget and

time constraints. They are intended for future improvement.

## 2.1 Primary Objectives

- Design and build a delta CNC machine
- Produce cheap electronics to control the machine
- Develop Kit like hardware / frame
- Develop a plotter attachment
- Develop a plastic extruder attachment

– PID controlled heater element

– Plastic filament feeder

- Allow for user configurations

– Vertical resolution

– set heat control

– Speed

- Develop Software

7

Project Objectives | 8

– STL to curve converter and slicer

– Computer Interface driver and software

– Command interpreter for printer (G-code)

## 2.2 Secondary Objectives

- LCD to show current status, settings and monitor variables
- Collapsable frame for easy transport (useful for demonstrations)
- Abstract hardware code to cross compile for AVR
- Experiment with substituting stepper motors with brushed motors and rotary hall

sensors

- Develop a solid dispenser attachment.

– Create edible objects with chocolate

– Print ceramics

## 2.3 Tertiary Objectives

- Design and demonstrate a a close to self replicating printer. Produce all compo-

nents except for the electronics.

- Implement an Ethernet add on

– Distributed printing service. Many printers can team and help build compo-

nents in parallel.

– Conveyor belt so that a queue of items can be constantly produced

- Add a Horizontal actuator attachment so that objects larger then the printing bed

can be produced

- Develop Plastic Recycler
- Wood/PCB router attachment

# Chapter 3

# Objective Strategy

Completion of the primary goals are essential to the projects success. To achieve each

task we must employ various project management skills such as progress monitoring,

development strategies, risk management and schedule planning.

## 3.1 Design Strategy

The hardware design will be in the form of a delta machine. These devices can per-

form fast accurate tasks as the light-weight print head is capable of quick acceleration.

This design has been adopted from a current reprap project<cite>5</cite>. The delta

machine will use less parts then a traditional Cartesian machine.

For a detailed overview of this projects design please refer to the Project Report

### 3.1.1 Hardware

Figure 3.1: Frame Design

9

Objective Strategy | 10

The frame will be constructed with aluminium beams. It have a small enclosed area for

the electronics and power supply. The printer bed is mounted on top of the case. There

is a beam on the top level that intersects the face in half. This is primarily for a place

to mount the plastic feeder but also serves as a structural support beam. The joins will

be printed on another 3D printer. Their design will facilitate modifications.

### 3.1.2 Electronic Systems

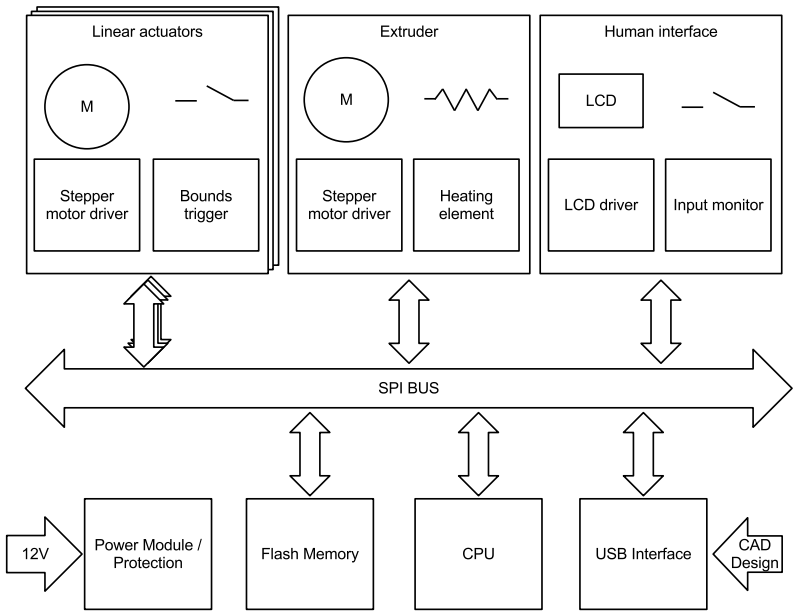
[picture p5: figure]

Figure 3.2: System block diagram

The electronics will consist of many smaller systems working in unison. This means we

require multiple low-powered microcontrollers opposed to one powerful central process-

ing unit. The system can be improved after it has been manufactured by connecting

additional devices to the SPI bus.

### 3.1.3 Software

Both software for a host computer and for the actual device will need to be developed.

A slicer application that breaks three dimensional CAD designs into multiple two di-

mensional frames is required. Drivers for connecting to the printer and communicating

with its sensors and diagnostics is essential. A simple protocol needs to be created that

allows a host computer to queue a CAD design for print is also needed.

Objective Strategy | 11

The printer needs to be able to translate the sliced CAD designs into instructions that

will command each actuator and allow the platform to follow a desired path. A control

system will need to monitor and manipulate the extruder temperature. Finally the

printer must be able to communicate with a host device.

## 3.2 Development strategy

The ’Agile Development’ method will be utilised during the project. It will help promote

fast and adaptive development. Agile development starts with a large list of tasks, these

are generally broken down into individual modular components.

An iterative process is performed once a week. It consists of:

1. Select the most valuable task from the global task list.
2. Analyse the task
3. Develop
4. Test
5. Integrate
6. After one week is over report back to supervisor

After an iteration the next week must be planned by:

1. Analyse the last tasks status
2. Review the whole projects status
3. Commit changes to production code base (if goals were satisfactory)
4. Plan next iteration (select more tasks or continue on current)
5. Reflect on supervisor’s feedback.

Objective Strategy | 12

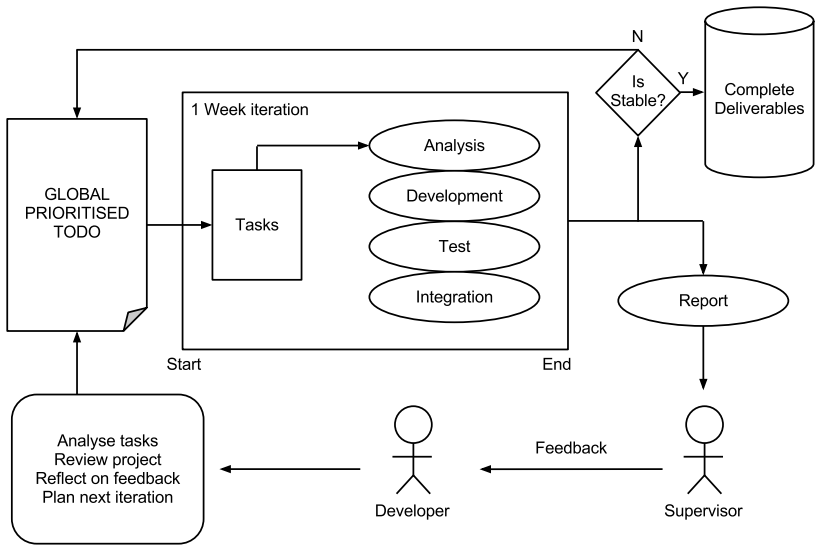
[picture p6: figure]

Figure 3.3: Agile Development Process

The benefit of a scrum like method is that it will allow us to be far more responsive to

unseen problems that may arise. The projects primary goals can possibly be modified

during project development if something does not go to plan or even if a new technology

/ discovery is made.

## 3.3 Risk Analysis

Risk mitigation is one of the most important aspects of managing a project. Possi-

ble predicted risks should be actively avoided. However not all are are forseen or are

avoidable, in such case we should attempt to minimise the impact.

### 3.3.1 List of risks

### 3.3.2 List of actions

Objective Strategy | 13
Risk (event) | Likelihood
(H/M/L)
| | Impact
(H/M/L)
| | | Ac-
| | | tion
Development starts late | M | L | 2
Schematics Incorrect | M | L | 1
PCB Incorrect | M | L | 1
Unobtainable parts | H | L | 3
Components break | H | M | 3
Underestimate Project time frame | M | H | 2
Underestimate Complexity | H | H | 4
Implementation does not function | M | M | 1
Incomplete project threat | L | H | 4
Code is lost / corrupted | L | L | 5
H-beams are not strong enough | L | M | 1

Table 3.1: List of possible risks

Action

Comment

1 | Diagnose and debug, attempt to develop work around depending on project
| stage. Redesign if problem is critical.
2 | Adjust Gantt chart, design new tactics and re-prioritise if required.
3 | Obtain new components. If unavailable or time frame does not permit,
| attempt to use alternative.
4 | Discontinue development on selected components. Adopt complete and tested
| consumer alternatives.
5 | Pull latest commit from off site Git repository server. Backups should be
| made nightly.

Table 3.2: List of actions

# Chapter 4

# Project Management

## 4.1 Important Dates

Date | Comment
March Mon 11th | Introduction to Project
April Weds 3 - Fri 5 | Mid semester Vacation
April Mon 8th | Project Plan due
June Tues 11th - Thurs 13th | Mid-Year Presentations
June Fri 14th | Journals due
July Fri 5 - Fri 26 | Mid-year Vacation
September Mon 30 - October Fri 4 | Mid-semester Vacation
October Mon 28th | Project Thesis due
October Weds 30th | Poster due
November Mon 4th - Weds 6th | Final Presentations & Demonstrations

Table 4.1: List of important dates

## 4.2 Schedule

A strict schedule must be kept to ensure successful completion of this project. I have

included a buffer month to help cater for unseen problems. If the project is completed

before this time I may attempt more of the secondary objectives. A second and third

revision might be possible if the iterations are kept on time. A third generation would

be ideal as it would represent a well configured device that has been thoroughly tested

and improved.

14

Project Management | 15

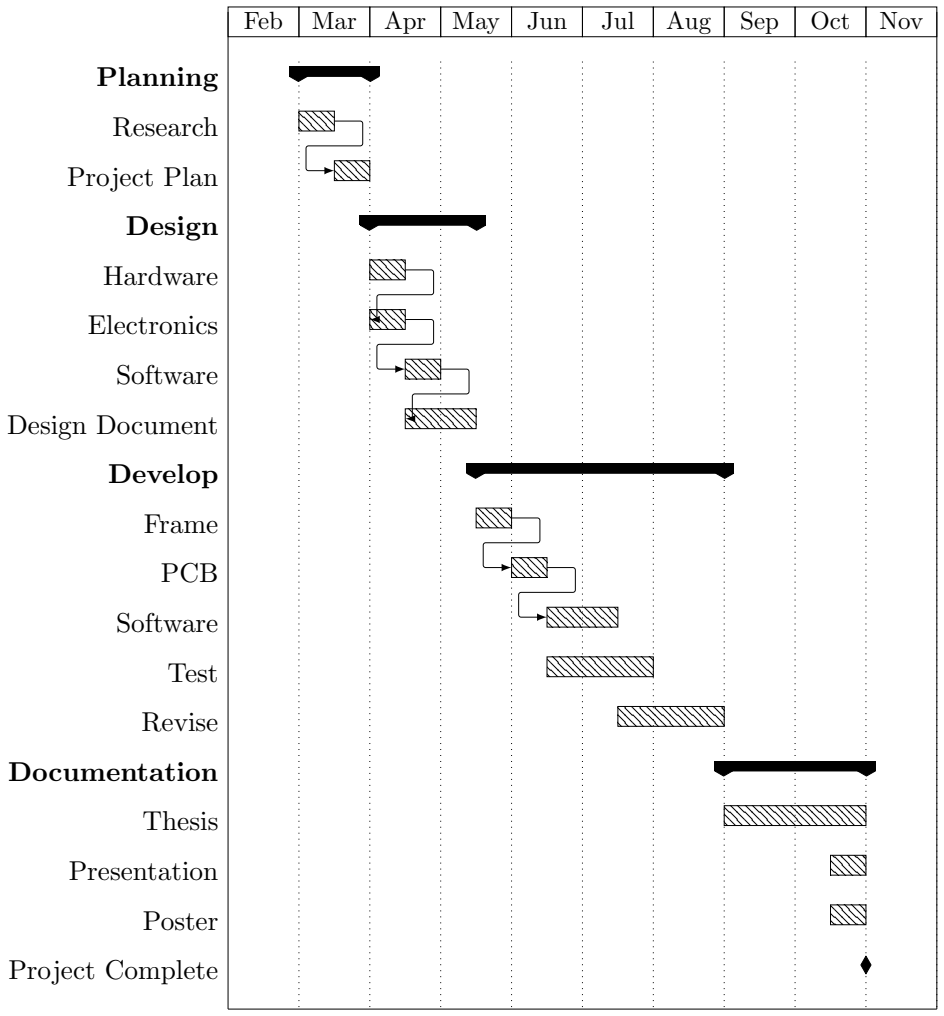
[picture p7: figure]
Feb; Mar; Apr May Jun; Jul; Aug; Sep; Oct; Nov; Planning; Research; Project Plan; Design; Hardware; Electronics; Software; Design Document; Develop; Frame; PCB; Test; Revise; Documentation; Thesis; Presentation; Poster; Project Complete

Figure 4.1: Gantt Chart

Project Management | 16

## 4.3 Budget

There are many consumer 3D printers on the market currently. They range from $450

to over $20,000. One of the primary goals of this project is to produce inexpensive

electronics to help reduce the overall cost of 3D printing. $450 is very competitive if

the quality is reasonable. The final target cost for this project is a base model for $300

AUD. I have considered many aspects that will help minimise costs:

- MSP430 value line microcontrollers
- Modular stackable mainboard
- Optional components: Flash memory, LCD and Ethernet.
- Minimal hardware
- Heavy gauge Fishing wire instead of typical belt drive
- Experiment with brushed motors instead of stepper motors
- Use common hardware store H section beam opposed to expensive general purpose

construction systems (motedis,system30,openbeam). Will require more complex

joins / drilling but at $5/m vs $25/m it is a safe investment.

### 4.3.1 Revenue

La Trobe University kindly provides a $200 spending budget for final year projects. I

will personally fund the remaining fees.

### 4.3.2 Expenses

The following resources should permit two iterations by recycling most parts.

### 4.3.3 Non-budgeted resources

Project Management | 17
Item | Cost
Aluminium Extrusions, joins and frame hardware | $100
PCB Fabrication | $50
Electronic components | $80
4 Stepper motors | $80
2kg ABS Plastic | $80
Extruder block | $20
Power supply | $30
Total | $450

Table 4.2: Budget allocation

Item | Provided By
MSP430 USB programmer dongle | Robert Ross
Host computer and development software | Keith Brown
Soldering equipment | Department of Electronics
| Engineering
CRO and testing equipment | Department of Electronics
| Engineering
Printed object cleaning tools | Keith Brown
Breadboard, Pliers, cutters, Multimeter and other general electronic items | Keith Brown

Table 4.3: Non-budgeted resources

# Chapter 5

# Conclusion

The macro and micro effects of an introduction to a personal manufacturing device is

fascinating. It has the possibility to facilitate innovation in many areas. Whether it is

a domestic or commercial application, 3D printing can help produce specialised parts,

reduce prototyping time and cost, promote first hand recycling and entice the next

generation into a technical field.

Low cost additive manufacturing is still in early development. A young underdeveloped

device or idea presents an opportunity for improvement. This technology will continue

to advance as demand increases. The delta style of 3D printers already is faster and

more accurate then the traditional Cartesian machines.

18

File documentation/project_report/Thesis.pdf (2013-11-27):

LA TROBE UNIVERSITY (http://www.latrobe.edu.au)

# Delta Printer Project Report

by

## Keith Brown

Final Year Project Report

in the
Faculty of Science, Technology and Engineering (http://www.latrobe.edu.au/scitecheng/) Department of Electronic Engineering (http://www.latrobe.edu.au/ee)

## November 2013

# Declaration of Authorship

La Trobe University | Department of Electronic Engineering

## Statement of Authorship INDIVIDUAL SUBMISSION

Please read the following instructions and associated University documents before completing and submitting this form with your item of assessment.
1. A Statement of Authorship must be completed for all items of assessment where the assessment is worth ten percent (10%) or more of the total for the unit.
2. The Academic Misconduct Policy found at http://www.latrobe.edu.au/policies
3. Statute 16 found at http://www.latrobe.edu.au/legalservices/statutes.html
4. Regulation 16.2 found at http://www.latrobe.edu.au/legalservices/regulations.html

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

i

LA TROBE UNIVERSITY (http://www.latrobe.edu.au)

# Abstract

Faculty of Science, Technology and Engineering (http://www.latrobe.edu.au/scitecheng/)

Department of Electronic Engineering (http://www.latrobe.edu.au/ee)

Bachelor of Electronic Engineering

by Keith Brown

This document describes the project plan for an inexpensive 3D printer. The project is

developed for the final year engineering project at La Trobe University by Keith Brown.

The printer will be in the form of a delta machine. The intention is to reduce the number

of components and utilise cheaper hardware while still achieving a fast accurate print.

The electronics will not be a direct derivative of current implementations. Experimen-

tation with alternative architecture will be trialled with the goal of delivering a more

computational capable system.

An introduction into 3D Printing and its concepts, advantages and issues is outlined.

The commercial viability for both commercial and consumer markets is described. This

projects primary, secondary and tertiary objectives are listed. The strategies to achieve

these goals is also described, followed by budget requirements and lastly a detailed

schedule is included.

# Acknowledgements

I would like to share my sincere gratitude to Professor Robert Ross, my primary su-

pervisor whom has given me so much creative control. Robert has provided constant

assistance. He also has bestowed me with his precious technical expertise. Adam Con-

sole my co-supervisor, has helped steer this project in the right direction on numerous

occasions. It was Adam that suggested the delta machine design. His diverse knowledge

is irreplaceable.

The RepRap community has paved the way for projects like this. There is a wealth of

freely available information on their website and forums. I hope that I will be able to

express my appreciation by giving something back to the open source community.

I would like to personally thank everyone who has supported me. I have discussed this

project with many of my friends and family, who have contributed with valuable support

and feedback.

iii

# Contents

Declaration of Authorship | i
Abstract | ii
Acknowledgements | iii
List of Figures | v
List of Tables | vi
1 Introduction | 1
2 Structure and motion analysis | 7
3 Motion | 14
4 Hardware | 15

iv

Contents | v
5 Electronic Systems | 18
6 Software | 19
7 Testing | 20

# List of Figures

1.1 Growth of CAD designs on thingiverse.com | | 5
2.1 Structure Diagram | | 8
2.2 Top view components with platform | 12

vi

# List of Tables

2.1 List of vectors | 8

vii

# Chapter 1

# Introduction

3D Printers have received a lot of media attention recently. Additive manufacturing has

been around for at least 30 years<cite>1, 2</cite>. However, in the last five years

popularity has increased dramatically due to the availability of much cheaper entry level

machines. It is now possible for the general public to purchase pre-assembled printers

at a similar cost as a personal computer.

There will always be innovation and dangers associated with a new technology. We

already have prime examples of both aspects; At a 2011 TED talk, Dr Anthony Atala

presented a human kidney prototype that his team had printed<cite>3</cite>. Late

2012 Cody Wilson uploaded a video to Youtube that showed himself firing a gun mostly

composed of 3D printed parts<cite>4</cite>.

The environment will benefit from this new way of producing products. Firstly, plastic

items can be recycled and reused to create new, more useful items. This not only

reduces costs but it also eliminates transportation of new items. They no longer need

to be imported and transported all over the country, they can just be downloaded.

Whilst companies like Objet and Stratasys produce printers for the commercial sector,

it is hobbyist style printers that have spread awareness of such technology. The Reprap

foundation has produced numerous models under the GPL licence. Their main goal is

to produce an affordable device that can self replicate. All of the designs are available to

download and print. Makerbot Industries is a comercial operation that was born from

an open source community.

Online services such as Shapeways provides 3D printing services. This allows their

customers to receive a higher quality print without investing in expensive hardware.

CAD design community sites have also been very popular such as ’thingiverse.com’.

1

Introduction | 2

There are over 30,000 free designs including a key-chain fob, mobile phone case, model

radial engine and even 3D printer parts and upgrades.

## 1.1 3D printing methods

Additive manufacturing is the process of constructing a three-dimensional object by

depositing material in discrete layers. Conversely, traditional machining methods are

subtractive; material is removed to expose the desired object. This printer utilises an

additive method as it produces fine plastic layers to build an object. There are many

different approaches of additive manufacturing. The main four methods are outlined in

the following paragraphs.

Fused deposition modelling or FDM is the method of extruding thermoplastics in layers.

This project is considered to use an FDM method as it extrudes fine plastic layers to build

an object. The printer deposits plastic material by melting it through a hot extruder.

The extruder resembles a metal funnel that takes solid plastic and produces liquid plastic

out of a small hole. The liquid plastic can be fused to previously deposited material. The

machine must physically move the extruder around an area, while placing plastic where

it is required. This process is repeated layer by layer to achieve a three-dimensional

object. The technology was invented by S. Scott in 1980 <cite>2</cite>.

Selective laser sintering or SLS is a technique that allows either metal, plastic, ceramic

and glass powder to be fused together with a powerful laser. The laser targets cross-

sections, selectively fusing a fine layer of powder to the object. Once a layer has been

complete, a fresh layer of powder is dusted over the object and the process repeats.

The left over material acts as a support for the object being manufactured. After the

procedure has finished, the excess powder can be removed and used for the next print.

The process is slow, producing porous but strong results.

Stereolithography or SLA is the method of using an ultraviolet light to cure a photopoly-

mer. The printing platform sits in a vat of liquid resin. The light targets a cross-section

of the desired object and the exposed resin will solidify. Once the layer has completed,

the platform will move down allowing for another layer to be added to the model. SLA

produces accurate results but is a very slow process. SLA has received a lot of attention

recently as the method has been adopted by a handful of young start ups. It offers a

much greater result compared to the current generation of FDM printers. However the

hardware and resin is very expensive.

Laminated object manufacturing or LOM is another rapid prototyping method. It uses

a laser or a knife to cut out layers from an adhesive-coated material. The layer is

Introduction | 3

then heated and pressed onto the previous layers. A new sheet of material is rolled in

place and the process repeats. This method can be relatively cheap as readily available

material such as paper can be used.

Each process is managed by a technique called ’computer numerical control’ or CNC.

This method is essentially computer controlled automation. Three-dimensional models

are developed using ’Computer aided design’ or CAD. These CAD models are processed

to produce CNC commands known as G-code. The G-codes are instructions that tell

the machine how to produce the CAD model.

## 1.2 FDM Articulation implementations

A Cartesian Gantry structure is the most common implementation. It consists of a

linear actuator for each axis of freedom. The horizontal plane generally has a sturdy rail

that a bridge is mounted on, this rail permits motion in the x direction. A carriage is

mounted to a rail that connects the bridge together. The carriage can move along this

rail and therefore permits motion in the y direction. Lastly the carriage has a tool that

is capable of actuating in and out in the z direction.

The Gantry system is a well tested framework and is industry standard. It can be

found in many applications from small desktop CNC machines to huge container cranes.

While the frame is very strong, each linear actuator is dependent on another. The bridge

actuator has to be the strongest as it must provide enough force to move the bridge,

carriage and tool. This becomes an issue for fast moving applications as the momentum

will be relatively large.

The Delta robot has three vertical rails placed in the formation of an equilateral triangle.

Each linear actuator moves in the same direction and has kinetic linkages that connect

each carriage to a central platform. This platform can be positioned by placing each

carriage at a certain height. This is an improvement over the Gantry setup because each

actuator shares the load equally. It is capable of faster speeds because there is less load

on the tool end.

## 1.3 FDM accuracy and materials

Currently, leading consumer 3D printers can produce objects with layers heights of 0.1

millimetres. Such an accurate print will generally take around five hours for a medium

sized print. Pricing for a mostly pre-assembled unit is around USD$2,200.

Introduction | 4

Currently there are two main types of plastics readily available for FDM printing. Firstly

Acrylonitrile Butadiene Styrene or ABS is a strong material. It is a oil based plastic that can be melted and extruded at a temperature of approximately 105 AřC. It is fairly ˆ

cheap at $40 a Kg. It does contract slightly as it cools.

Polylactic Acid or PLA is another alternative that can be used for FDM printing. It

is marginally less expensive then ABS. While being more brittle then ABS it does not

contract as much. PLA is a biodegradable polymer and actually is produced by corn

starch. Because of it’s lower melting point it is not ideal for applications related to heat.

## 1.4 Proposed Solution

The delta machine design has been adopted for this project. Recently the Rostock

project has spawned many derivatives, most achieving cheaper construction over the

last generation of reprap printers. Delta machines have been used for many applications

including; pick and placers, packaging and production line sorters.

Its simplicity helps reduce hardware costs. But the biggest advantage is the machines

speed and accuracy. If the central platform is kept light, fast acceleration can be main-

tained. This permits the machine to perform in a sporadic manner while maintaining

an accurate position.

The electronics system will not be a derivative of current implementations. I will ex-

periment with different architectures with the goal of producing a much cheaper but

fully capable system. The components will be made modular to allow for a high level of

customisation. This helps to keep the main-board costs low but still permits additional

more expensive upgrades such as a Ethernet add on.

## 1.5 Commercial Viability

This old technology is becoming established in a new market. While it becomes more

accessible, new opportunities begin to emerge and intern, increases demand. Prices are

decreasing, materials are becoming more accessible and there is an increasing amount of

printable designs being uploaded to the Internet. The later attributes the most positive

influence to the 3D printing market. This makes an old product more valuable.

Introduction | 5

●●●●●●●●●●●●●●●●●●●●●●●●●●●

●●●●

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
2009 | 2010 | 2011 | 2012 | 2013

0 5000 10000 15000 20000 25000 30000

## Growth of items uploaded to Thingiverse

Time (years)

Number of new items uploaded

Figure 1.1: Growth of CAD designs on thingiverse.com

It is clear that this market is expanding at a promising rate. Furthermore because there

is such a diverse range of neighbouring markets that will benefit from this technology,

it is likely that it will be supported by commercial demand alone. Applications for 3D

printing have yet to be completely discovered, the boundaries are always being pushed

by innovators. It is apparent that a very successful industry has been created.

### 1.5.1 Commercial Market

3D printing can help many different businesses. For example; Product designers can

produce prototypes within a few hours, prosthetics can be made for a person more fre-

quently and engineers can produce custom parts easily. It is important to note that

even if a 3D printer existed in every home, there are still many skills that can’t be

replaced by automation. Downloading a generalised product will never replace a profes-

sionally crafted custom version. 3D printing just streamlines the development cycle and

promotes rapid growth.

Introduction | 6

Rapid prototyping reduces development costs and creates new opportunities. It is possi-

ble that we will see a rise in hardware start-ups similar to the influx of software start-ups

we have seen recently. It may be more feasible for a young company to attempt entering

into established markets with little overhead.

### 1.5.2 Consumer Market

There is a number of reasons why an individual might desire a 3D printer. It may help

reduce our consumption rate by allowing us to easily repair broken household items.

While it is unlikely for the average person to need a miniature factory, it is ideal for

hackers, hobbyists, artists and craftsmen

Currently, the largest consumer market for 3D printing falls inside the open source

community. Although intellectual property is freely shared, support and labour is very

valuable. These customers are generally open to early adoption of new technology. The

network of passionate, diversely skilled customers strive to improve the current designs

and collaboratively innovate the CNC scene.

# Chapter 2

# Structure and motion analysis

## 2.1 Structure

A delta machine consists of a number of kinetic chains that meet at a central platform.

This platform can be moved by actuating the pivots connected to the main structure.

The platform is kept parallel to the floor during motion. [Figure 2] represents a simple

two armed delta machine. The two-dimensional diagram helps to illustrate the important

lengths and vectors. After we have analysed a two dimensional machine we will apply

these concepts to three-dimensions.

7

Structure and motion analysis | 8

fig/structure_positioning//img/structure_diagram.pdf

Figure 2.1: Structure Diagram

——- | —————————————————————
İSń | Horizontal length of the frame ´
İSş | Vertical length of the frame ´
İSČ | Height of the actuator pivot point from the origin ´
İSL’ | Length of the kinetic linkage ˇ
İŞG | Radius of the platform ˘
İSŠ | Position of the extruder tip or centre of the platform ´
İSű | Origin of the system ´
İSŽ | Horizontal vector ´
İSŽ | Vertical vector ˇ
İSŽ | Depth vector ˙
——- | —————————————————————

Table 2.1: List of vectors

The following assumptions are made to help define the system:

- Platform and linkages must stay within the frame’s outer rails.

Structure and motion analysis | 9
- Linkages are not restricted in any way, they may swivel on their joins in any

direction.

- The platform can not move down into the base.
- Linkages are restricted to the rail’s length.
- Linkages can not stretch or contract.

## 2.2 Simple one dimension motion

Lets consider one dimension to begin with, Figure 1 illustrates the movement of three

key points; the platform and the left and right linear actuators. We can see that if the

linkages are the same length as the vertical distance, the platform is capable of reaching

any position along the x axis.

Simple ideal motion Also, it can be seen that a vertical actuator requires an equal amount

of travel to permit full movement. It is important to note that the platform is considered

a point source in this example. Practically this is not the case as we will require a place

to mount tools.

For a desired position of İSŠ( ´ İSŽ), we need to derive where to place linear actuators. ´

Take figure [3] below, lets derive the equations that will translate a desired İSŽ into ´

İSČâ´ CÁ and ,

İSČâ´ CĆ. ´

Simple one dimension parameters Firstly, lets derive relationship between İSŽ and ´

İSČâ´ CÁ: (1) ,
h

2 = a

2
1+b

2
1 ⇔ a1 =

p
h

2 − b
2/1(2)x = b1−D/2 ⇔ b1 = x+D/2 substituting
(1) into (2) gives a1(x) = p h

2 − (x + D/2)² Now, lets find the relationship between
İSŽ and ´ | İSČâ´ CĆ: (3) ´ | h
2 = a

2
2 + b

2
2 ⇔ a2 =

p
h

2 − b
2/2(4)b2 = D − b1 substituting (2)

into (4) gives b2 = D − (x + D/2) ⇔ b2 = D/2 − x finally, substituting (4) into (3)
a2(x) = p | h
2 − (D/2 − x)

2

## 2.3 Platform

We now need to consider what happens to the linkages when they are offset by the

platforms width.

Simple platform By adding extra length to the horizontal component, we have decreased

the horizontal outer bounds of the system. The smaller the platform the more room we

are able to travel. It should also be noted that the larger the platform, the less vertical

travel is required for the actuators.

Structure and motion analysis | 10

The Platform reduces the b1 and b2 term in our position equation by r. We now have: a1(x) = p
h

2 − (x + D/2 − r)

2 a2(x) = p
h

2 − (D/2 − x − r)

2

## 2.4 Vertical travel constraints

We can also reduce the vertical travel required by reducing the linkages length. This

intern reduces the available printing area. However, this can be used to our advantage.

For example if we needed to restrict the horizontal bounds so that the platform can’t

physically interfere with the belt drive that runs alongside the vertical rails.

Variable linkage length

## 2.5 Two dimensional motion in the vertical plane

Now we are able to examine how we may add a vertical component to the system. From

the last sections we discovered that the length required for the vertical actuators is the

equal the linkages length. In this example, we have created a square printable area of (

İSL’-2 ˇ | İŞG) ˘ Aš. This is possible as the rails are twice the length of the linkages length ˆ
or İSş = 2( ´ | İSL’-2 ˇ | İŞG). ˘

Two dimensional motion Introducing the z component directly adds to the a1 and a2 terms. The position equations are amended as: a1(x, z) = p
h

2 − (x + D/2 − r)

2 + z
a2(x, z) = p | h
2 − (D/2 − x − r)

2 + z

## 2.6 Two dimensional motion in the horizontal plane

Now its time to examine how adding a third actuator allows for two dimensional move-

ment in the horizontal plane. Figure [8] is a top-down view of our system. The actuators

are placed in a equilateral triangle formation to distribute the load evenly. The posi-

tion of the platform can be altered by changing the lengths of the linkages horizontal

component, the b term. Remember, this is not stretching the linkages, it is merely dis-

placing length between the horizontal and vertical component - the hypotenuse remains

the same. By looking straight down into the system, only the b vectors are visible, the

carriages on the rails or the a term is directed in/out of the page.

The coordinates system has been aligned with the actuators to help simplify the problem.

The origin is placed at the centre of the print bed. Please note that the print bed is

Structure and motion analysis | 11

represented as a circle with its radius equal to the minimum distance from the origin to

the frame. The printer is actually capable of printing in a slightly rounded three point

triangle (see figure[9]), but to help visualise and simplify the system we have selected a

circular print bed.

x and y motion To control the platforms position we must modify the carriages vertical

position a. However, the horizontal plane position is completely dependent on b. We

have already established the relationship between a and b, and that is a =

√
h
| 2 − b
| 2.

We now need to develop the relationship between b and the position (x, y).

Each actuator will have its own equation for calculating its b term. This is because they

are not placed uniformly around the coordinates system even though they are equally

apart. Firstly, the general rule for calculating b as a function of the platforms position:

bn(x, y) = |

−−−−−−−→
RnP(x, y)| Where R is the position vector of the target actuator and P is

the position vector of the platform.

[Top view components] (/img/top-viewdiagram.svg)

Figure [8] illustrates that this problem can be solved by a simple application of Pythago-

ras’ theorem again.

Top actuator: d1(x) = x e1(y) =

√
3
3 D−y b1(x, y) = p
d

2
1 + e

2/1 b1(x, y) = q
(x

2 +

√
3
| 3 D − y)

2

Bottom left actuator: d2(x) = 1 2D+x e2(y) =

√
3

6 D+y b2(x, y) = q
(

1
2D + x)

2 + (

√
3
6 D + y)

2

Bottom right actuator: d3(x) = 1 2D−x e3(y) =

√
3

6 D+y b3(x, y) = q
(

1
2D − x)

2 + (

√
3
6 D + y)

2

Structure and motion analysis | 12

## 2.7 Platform in the horizontal plane

fig/structure_positioning//img/top-view-platform_diagram.pdf

Figure 2.2: Top view components with platform

Adding a platform with a radius of r just offsets our x and y components as seen in

figure [9]. The amended equations are:

a1(x, y) = q
(

√
3
3 D − y+r)

2 + x

2 a2(x, y) = q
(

1
2D + x−

1/2 r)

2 + (

√
3
6 D + y−

√
3
2

r)

2 a3(x, y) =
q
(

1
2D − x+

1/2 r)

2 + (

√
3
6 D + y−

√
3
2

r)

2

## 2.8 Three dimensional motion

Both horizontal and vertical components have been explained and now can be combined

into one system. To implement a three dimensional system, we simply need to replace our

bn variable in the vertical plane equation with the horizontal plane equations. The result is: a1(x, y, z) = q
(

√
3
3 D − y + r)

2 + x

2+z a2(x, y, z) = q
(

1
2D + x −

1/2 r)

2 + (

√
3
6 D + y −

√
3
2

r)

2+
z a3(x, y, z) = q
(

1
2D − x +

1/2 r)

2 + (

√
3
6 D + y −

√
3
2

r)

2 + z

Structure and motion analysis | 13

## 2.9 Constraints

### 2.9.1 Printing Bed

A design assumption was made at the beginning of this section; The platform can not

be positioned outside of the frame. To force this rule to apply, we must set the linkages

length equal to the minimum distance from a rail to a side of the frame. The maximum

length required is a line straight down the y axis from the rail to the frame which is

equal to

√
3
2 D. If we swing the platform around, pushing it to the maximum radius that

this length permits, we see that the path is not actually a circle but a rounded triangle.

The light blue path in figure [11] is the maximum positions. Such an unusual path is

typically not needed, so we will simplify our problem by using a circular print bed (dark

blue line in figure [11].

Printbed range To allow for a platform, we must subtract its radius from each of the

linkages length. So, our rule for h is: h =

√
3
2 D − r

### 2.9.2 Universal Joint Angle Range

Universal joint angle horizontal range The universal joints that will pivot to allow full

movement will need to be capable of a certain range. This can be calculated exactly

with:

θ = 60 − 2 arctan (

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
Practically, we can simplify the problem by aiming for 60◦ in the horizontal direction and 90◦
in the vertical direction.

# Chapter 3

# Motion

14

# Chapter 4

# Hardware

Now that we understand the physical constraints we can start to design the physical

system. Firstly, lets reiterate over some of the main objectives that relate to this section:

- Kit like assembly
- Cheap hardware
- Solid and sturdy construction

## 4.1 Frame

We have selected two possible struts to build the framework. Both are made of alu-

minium so are reasonable light.

System30 Beam Positives

- Very strong in any direction
- Simple mounting and joining
- Reusable
- Easy to modify / tune

Negatives

- Expensive at $25 per meter
- Hard to source

15

Hardware | 16

H-Beam Positives

- Very strong in the vertical direction
- Cheap at $5 per meter
- Easy to obtain

Negatives

- Flexes in the horizontal direction
- Will have to drill to mount securely

Currently, the prototype material has not been decided. The H-Beam offers a signif-

icant reduction in price, and those savings can be passed on to other aspects of the

project. However, System30s provide a better investment during the prototyping phase

as they can be easily modified throughout the project. It should also be mentioned that

System30 like beams are generally used for CNC machines, especially hobbyist versions.

Frame Design The frame will have a small enclosed area for the electronics and power

supply. The printer bed is mounted on top of the case. There is a beam on the top level

that intersects the face in half. This is primarily for a place to mount the plastic feeder

but also serves as a structural support beam.

We will need to know how much material to order. There is 3 equilateral triangles with

side lengths of D and there are 3 rails that need to be of 2D + 3 ∗ .03. The later 0.03 is

to allocate room for an enclosure so that we can maintain a symmetrical print area. But

for practiacle purposes, we will not consider the extra length so that it is possible to use

a multiple of the original materials length. M = 3(3D)+ 3(2D)+

√
3
2 D M = (15+

√
3
2

)D

Now, we need rewrite this by substituting the relationship between D and the print bed radius b. D = 2√
3(b + r) M(r, b) = (15 +

√
3
2

)(2√
3(b + r)) To minimise waste, D needs

to be a multiple of the purchased material’s length. The H-Beam comes in one and three

meter lengths. To further reduce waste, the purchased length should be close to a whole

number.

Hardware | 17

## 4.2 Frame Brackets

## 4.3 Platform

## 4.4 Linkages

## 4.5 Linear Actuators

### 4.5.1 Belt Drive

### 4.5.2 Motors

## 4.6 Tool End

### 4.6.1 Plotter

### 4.6.2 Dispenser

### 4.6.3 Extruder and Feeder

# Chapter 5

# Electronic Systems

## 5.1 Methodology

## 5.2 Microcontroller

## 5.3 Motor Drivers

## 5.4 Communication

## 5.5 Sensory input

## 5.6 Power

## 5.7 Safety

18

# Chapter 6

# Software

## 6.1 Major Functions

## 6.2 Major Constraints

## 6.3 High Level Diagrams

## 6.4 Device Abstraction

## 6.5 Sequence Analysis

## 6.6 Framework

## 6.7 Implementation

### 6.7.1 Portability Header

### 6.7.2 G code interpreter

### 6.7.3 Positioning

### 6.7.4 Motion

19

# Chapter 7

# Testing

20

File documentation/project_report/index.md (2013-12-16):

#define university LA TROBE UNIVERSITY
#define university_link http://www.latrobe.edu.au
#define faculty Faculty of Science, Technology and Engineering
#define faculty_link http://www.latrobe.edu.au/scitecheng/
#define theme thesis
#define department Department of Electronic Engineering
#define department_link http://www.latrobe.edu.au/ee
#define title Delta Printer Project Report
#define subtitle Final Year Project Report
#define author Keith Brown
#define author_email k9brown@students.latrobe.edu.au

#(head.tex)
#(title.tex)
#(declaration.tex)
![abstract.md]
#(acknowledgements.tex)
#(headers.tex)
#(contents.tex)
#(figures.tex)
#(tables.tex)
#(main.tex)

![intro]
![structure_positioning]
![motion]
![hardware]
![electronics]
![software]
![testing_results]
![management]
![conclusion.md]

![appendices]
#(bibliography.tex)
#(end.tex)

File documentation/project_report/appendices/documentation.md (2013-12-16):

\chapter{Reference Documents}
\label{AppendixA}
\lhead{Appendix A. \emph{Reference Documents}}

Existing Documentation
======================

- Keith Brown. Delta printer Project Plan: April 2013
- La Trobe University. ELE4EPA/EPB Subject learning guide: Marth 2013

Vendor Documentation
====================
- TI. MSP430x2xx Family Guide. [http://www.ti.com/lit/ug/slau144i/slau144i.pdf]([http://www.ti.com/lit/ug/slau144i/slau144i.pdf): January 2012
- Atmel. ATmega644 Series Guide. [http://www.atmel.com/Images/doc2593.pdf](http://www.atmel.com/Images/doc2593.pdf): January 2012

Other Documentation
===================
- Reprap Foundation website/forum [http://reprap.org/](http://reprap.org/): March 2013
- Brian W. Kernighan and Dennis M. Ritchie. The C Programming Language, Second Edition. Prentice Hall, Inc., 1988.

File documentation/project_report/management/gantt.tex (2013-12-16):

\begin{figure}[p]

  \begin{gantt}{20}{12}
    \begin{ganttitle}
     \titleelement{Feb}{1}
      \titleelement{Mar}{1}
      \titleelement{Apr}{1}
      \titleelement{May}{1}
      \titleelement{Jun}{1}
      \titleelement{Jul}{1}
      \titleelement{Aug}{1}
      \titleelement{Sep}{1}
      \titleelement{Oct}{1}
      \titleelement{Nov}{1}
      \titleelement{Dec}{1}
      \titleelement{Jan}{1}
    \end{ganttitle}
    \ganttgroup{Planning}{1}{1}
    \ganttbar{Research}{1}{.5}
    \ganttbarcon{Project Plan}{1.5}{.5}
    \ganttgroup{Design}{2}{1.5}
    \ganttbar{Hardware}{2}{.5}
    \ganttbarcon{Electronics}{2}{.5}
    \ganttbarcon{Software}{2.5}{.5}
    \ganttbarcon{Design Document}{2.5}{1}
    \ganttgroup{Develop}{3.5}{8}
    \ganttbar{Frame}{3.5}{3.5}
    \ganttbarcon{PCB}{4}{.5}
    \ganttbarcon{Software}{4.5}{7}
    \ganttbar{Test}{8.5}{3}
    \ganttbar{Revise}{5.5}{6}
    \ganttgroup{Documentation}{7}{2}
    \ganttbar{Thesis}{7}{2}
    \ganttbar{Presentation}{8.5}{.5}
    \ganttbar{Poster}{8.5}{.5}
    \ganttmilestone{Project Complete}{11.5}
  \end{gantt}

  \centering
  \caption{Gantt Chart}
  \label{fig:figure3}
\end{figure}

\clearpage

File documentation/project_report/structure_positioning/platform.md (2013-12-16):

Platform
========

We now need to consider what happens to the linkages when they are offset by the platforms width.

//[Simple platform](svg:2)

By adding extra length to the horizontal component, we have decreased the horizontal outer bounds of the system. The smaller the platform the more room we are able to travel. It should also be noted that the larger the platform, the less vertical travel is required for the actuators.

The Platform reduces the #b_1# and #b_2# term in our position equation by #r#. We now have:
## a_1(x) = \sqrt{ h^2 - (x + D - r)^2 }##
## a_2(x) = \sqrt{ h^2 - (x - D + r)^2 } ##

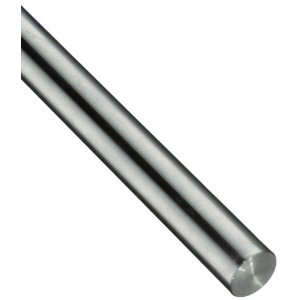
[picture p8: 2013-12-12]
documentation/project_report/hardware/8mm_linear_rod.jpg

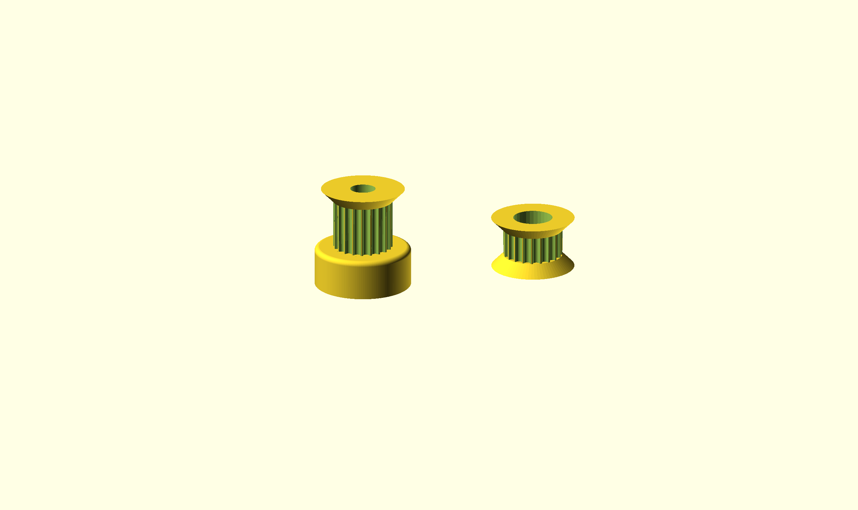
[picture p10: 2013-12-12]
documentation/project_report/hardware/gear.png

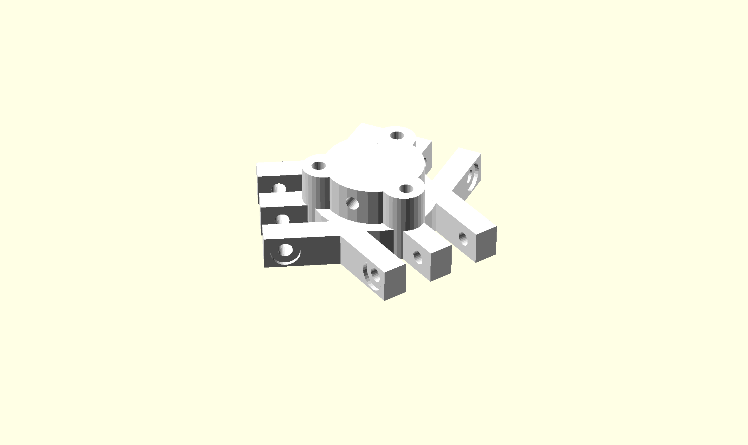
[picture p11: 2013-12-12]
documentation/project_report/hardware/tool_end/plotter.png

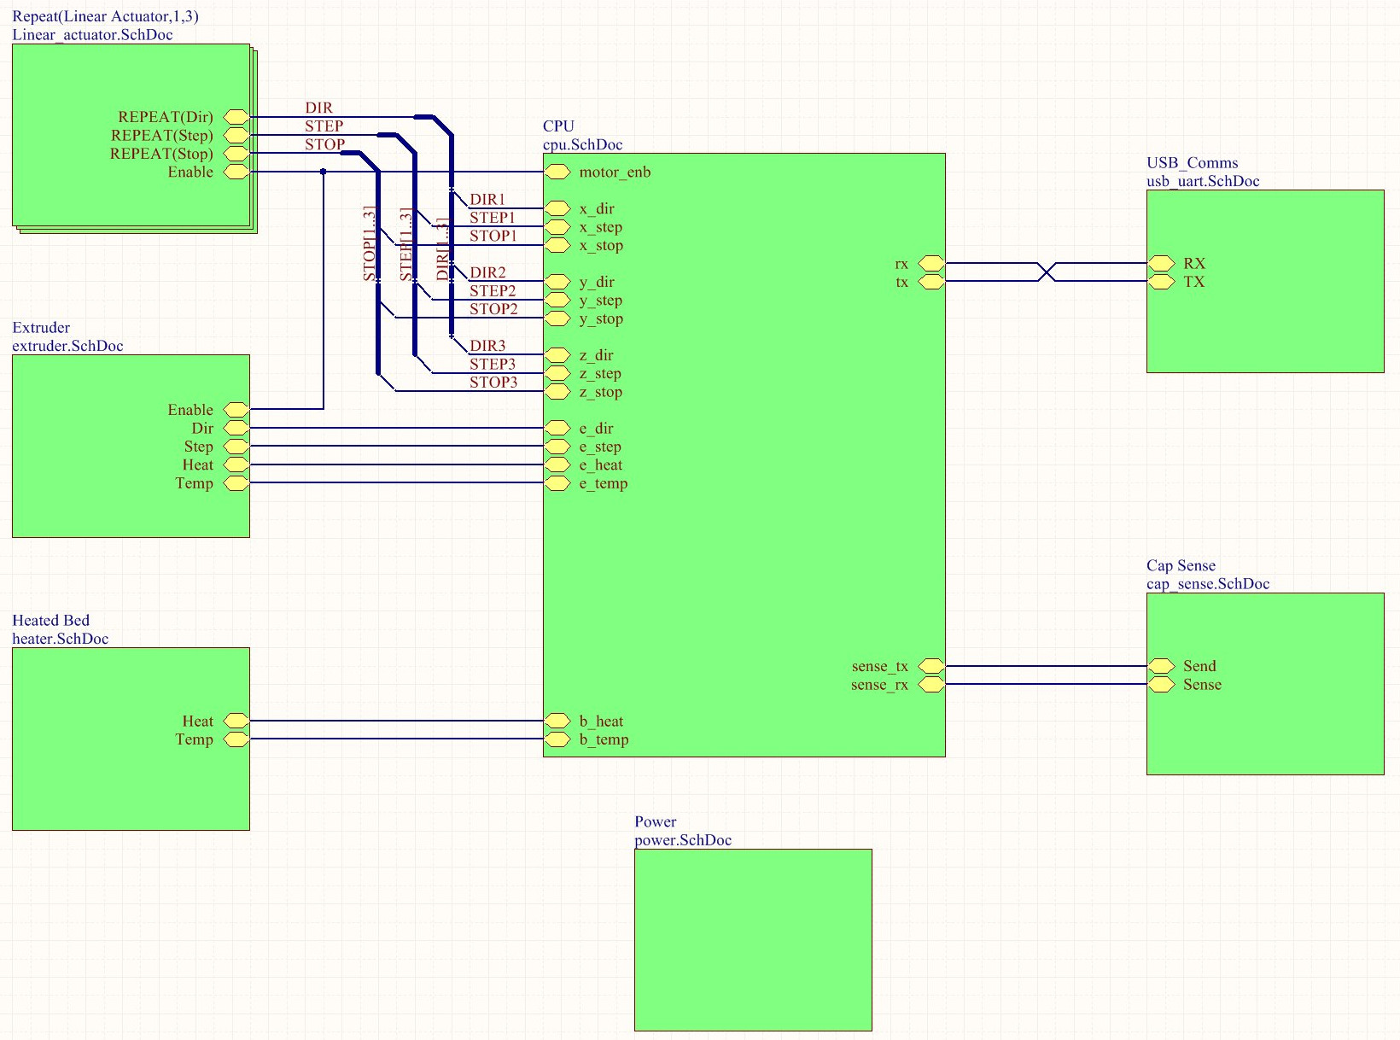
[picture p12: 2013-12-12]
documentation/project_report/electronics/top_level.jpg

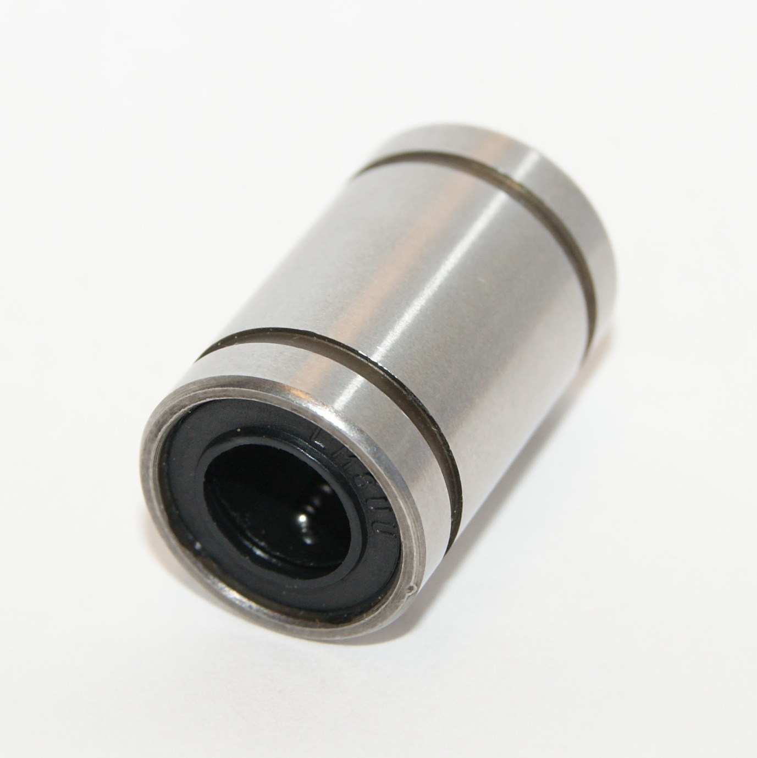
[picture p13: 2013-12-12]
documentation/project_report/hardware/LM8UU_Bearing.jpg

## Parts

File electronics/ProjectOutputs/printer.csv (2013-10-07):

Comment | Description | Designator | Footprint | LibRef | Quantity | Value
Res | Resistor 0805 | R1, R2, R8_LinearActuator1, R8_LinearActuator2, R8_LinearActuator3, R9_LinearActuator1, R9_LinearActuator2, R9_LinearActuator3, R15, R17_stepper1, R17_stepper2, R17_stepper3, R17_stepper4 | J1-0603 | Res | 13 | 220R | 603 | 2073428 | 0.003 | x
Res | Resistor 0805 | R3, R10_LinearActuator1, R10_LinearActuator2, R10_LinearActuator3, R12, R25 | J1-0603 | Res | 6 | 10K | 603 | 2073356 | 0.002 | x
Res | Resistor 0805 | R4_Heated Bed, R4_Hot End | J1-0603 | Res | 2 | 4K7 | 603 | 2073514 | 0.004 | x
Res | Resistor 0805 | R5_Heated Bed, R5_Hot End, R7_Heated Bed, R7_Hot End, R14 | J1-0603 | Res | 5 | 1K | 603 | 2073354 | 0.004 | x
Res | Resistor 0805 | R6_Heated Bed, R6_Hot End, R20, R23 | J1-0603 | Res | 4 | 270R | 603 | 2074225 | 0.004 | x
Res | Resistor 0805 | R11 | J1-0603 | Res | 1 | 49.9k | 603 | 2059470 | 0.002 | x
Res | Resistor 0805 | R13 | J1-0603 | Res | 1 | 15.8k | 603 | 2073398 | 0.005 | x
Res | Resistor 0805 | R18_stepper1, R18_stepper2, R18_stepper3, R18_stepper4, R19_stepper1, R19_stepper2, R19_stepper3, R19_stepper4 | C1206 | Res | 8 | 0.1R | 1206 | 2328138 | 0.1 | x
Res | Resistor 0805 | R21, R22 | J1-0603 | Res | 2 | 27R | 603 | 2074231 | 0.006 | x
Res | Resistor 0805 | R24 | J1-0603 | Res | 1 | 1M | 603 | 2073358 | 0.002 | x
RES_POT |  | R16_stepper1, R16_stepper2, R16_stepper3, R16_stepper4 | RES_SMD | RES_POT | 4 | 10K |  | 1689863 | 0.45
Cap Pol | Polarized Capacitor (Axial) | C9 | Capacitor Nichi CL 10x10 | Cap Pol | 1 | 470uF 25V | 10mm Can | 9695800 | 1.89 | x
Cap | Capacitor | C1, C2 | CAPC2012L-3D | Cap | 2 | 18pF | 805 | 1759194 | 0.029 | x
Cap | Capacitor | C3, C4, C5, C6, C7, C8_Heated Bed, C8_Hot End, C13_stepper1, C13_stepper2, C13_stepper3, C13_stepper4, C19, C20 | 1608[0603] | Cap | 13 | 100nF | 603 | 1844241 | 0.019 | x
Cap | Capacitor | C10, C15_stepper1, C15_stepper2, C15_stepper3, C15_stepper4, C16 | 1608[0603] | Cap | 6 | 10nF | 603 | 1709947 | 0.05 | x
Cap | Capacitor | C11 | CAPC2012L-3D | Cap | 1 | 22uF 6.3V | 805 | 2309030 | 0.168 | x
Cap | Capacitor | C12 | CAPC2012L-3D | Cap | 1 | 10uF | 805 | 2309029 | 0.075
Cap | Capacitor | C14_stepper1, C14_stepper2, C14_stepper3, C14_stepper4, C22, C23 | 1608[0603] | Cap | 6 | 100pF | 603 | 8819866 | 0.009
Cap | Capacitor | C17, C18 | 1608[0603] | Cap | 2 | 47pF | 603 | 1582668 | 0.009
Cap | Capacitor | C21 | 1608[0603] | Cap | 1 | 4.7uF | 603 | 2354102 | 0.11
Ferrite Bead |  | FB1, FB2 | 603 | Ferrite Bead | 2 | - | 603 | 1515699 | 0.013 | x
D Schottky | Schottky Diode | D5, D6 | DO-214-AA | D Schottky | 2 |  |  | 2301798 | 0.72
Fuse | Fuse | F1 | Fuse Holder | Fuse | 1
Inductor | Inductor | L1 | Inductor 5020 | Inductor | 1 | 10mH |  | 2309155 | 0.87
power_jack |  | P5 | PowerJack | power_jack | 1 |  |  | 185451401 | 1.75
USB Micro B |  | P8 | USB micro B | USB Micro B | 1 |  |  | 2293836 | 0.945
QNPN | NPN Bipolar Transistor | Q1_LinearActuator1, Q1_LinearActuator2, Q1_LinearActuator3 | SOT-23B_N | QNPN | 3 |  |  | 1798052 | 0.035
MOSFET-N | N-Channel MOSFET | Q2, Q3 | SOT23 | MOSFET-N | 2 |  |  | 1081307 | 0.178
LED3 | Typical BLUE SiC LED | D1, D2, D3_Heated Bed, D3_Hot End, D10, D11 | LED 0805 | LED3 | 15 |  | 805 | 2099236 | 0.129
Tactile Switch 6mm |  | SW1 | Switch 6mm | Tactile Switch 6mm | 1 |  |  | 1712975 | 0.21
DPDT | Switch | SW2 | MCLSS22 | DPDT | 1 |  |  | 1522046 | 0.52
ATmega644PA-AU | 8-bit AVR Microcontroller, 64KB Flash, 2KB EEPROM, 4KB SRAM, 44-pin TQFP, Industrial Grade (-40°C to 85°C) | U1 | 44A_N | ATmega644PA-AU | 1 |  |  | 1972106 | 13.97
irf8714pbf |  | U2_Heated Bed, U2_Hot End | SO-8_M | irf8714pbf | 2 |  |  | 1013430 | 0.215
AOZ1280 |  | U3 | SOT23-6 | AOZ1280 | 1
DRV8825 |  | U4_stepper1, U4_stepper2, U4_stepper3, U4_stepper4 | DVR | DRV8825 | 4 |  |  | 1903642 | 7.86
FT230XS |  | U5 | SSOP16_N | FT230XS | 1 |  |  | 2081321 | 2.84
ABMM2 |  | Y1 | ABMM2 | ABMM2 | 1 |  |  | 1611798 | 0.358
Buzzer |  | BZ1 | buzzer | Buzzer | 1

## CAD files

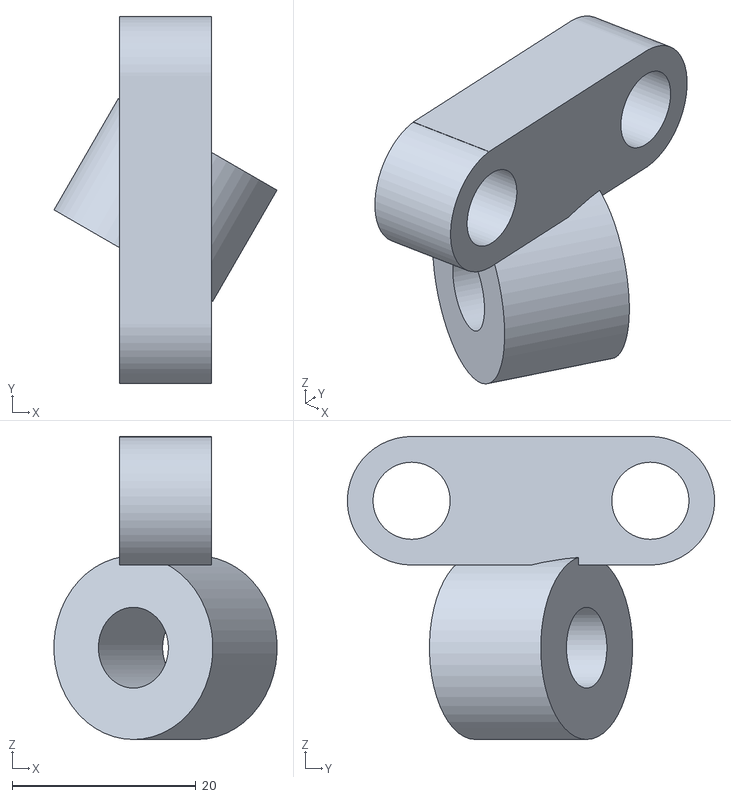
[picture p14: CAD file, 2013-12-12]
hardware/belt_delta/linear_actuator/strut_right.stl
24.3 x 40.0 x 33.0

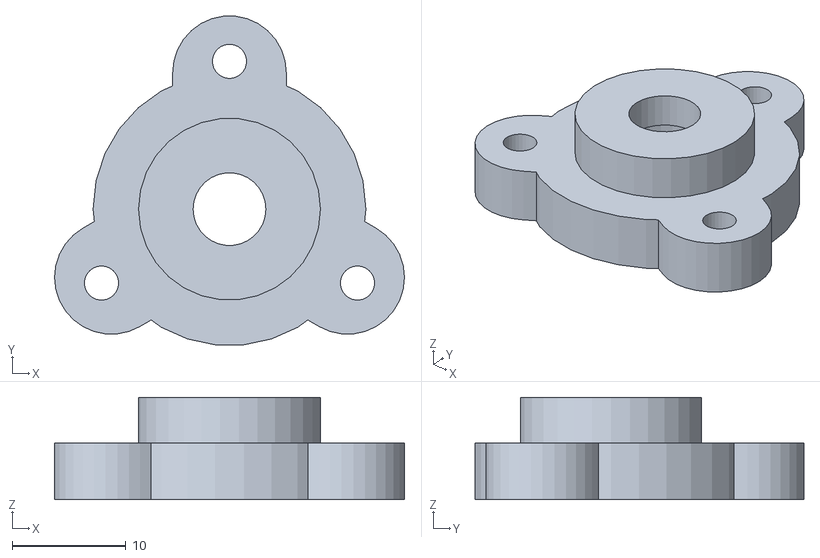
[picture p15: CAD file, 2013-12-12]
hardware/feeder/tube_coupler.stl
30.8 x 28.9 x 9.00

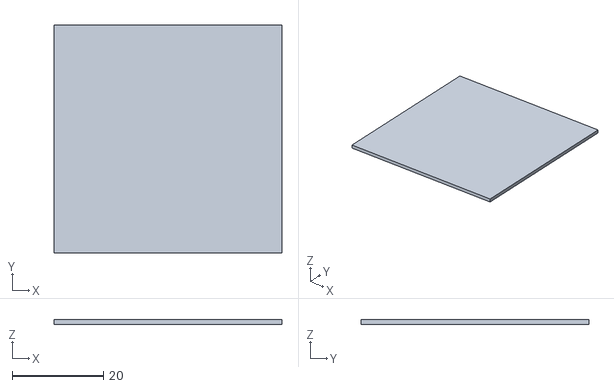
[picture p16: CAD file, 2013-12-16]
software/transmitter/box/box.stl
50.0 x 50.0 x 1.00

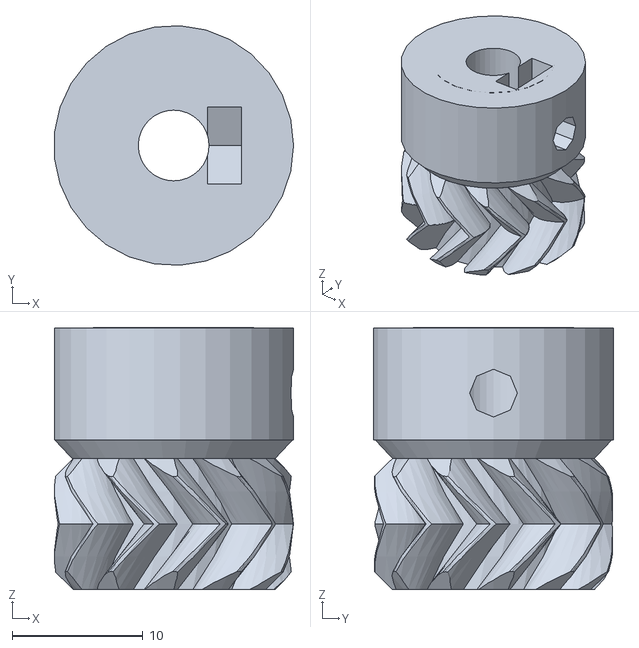
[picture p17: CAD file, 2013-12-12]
hardware/feeder/herringbone-gear-small.stl
18.3 x 18.3 x 20.0

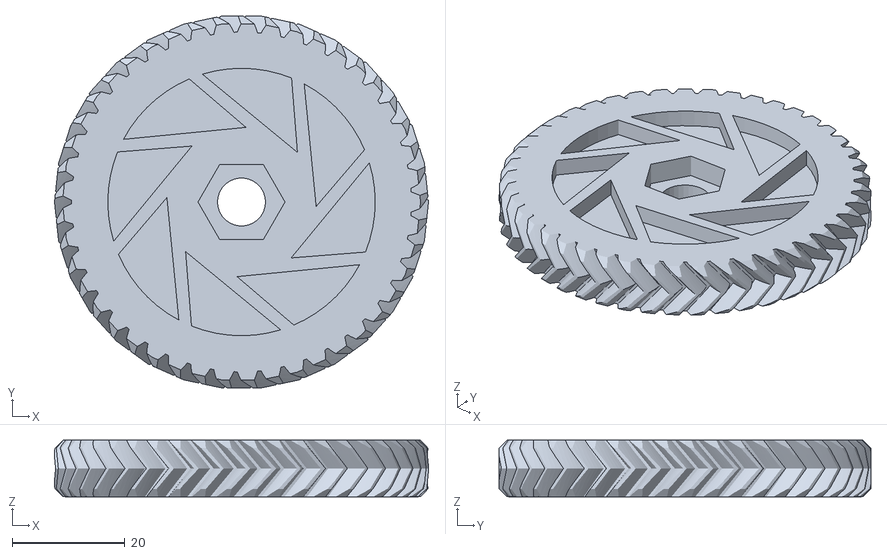
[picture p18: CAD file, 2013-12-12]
hardware/feeder/herringbone-gear-large.stl
66.2 x 65.9 x 10.0

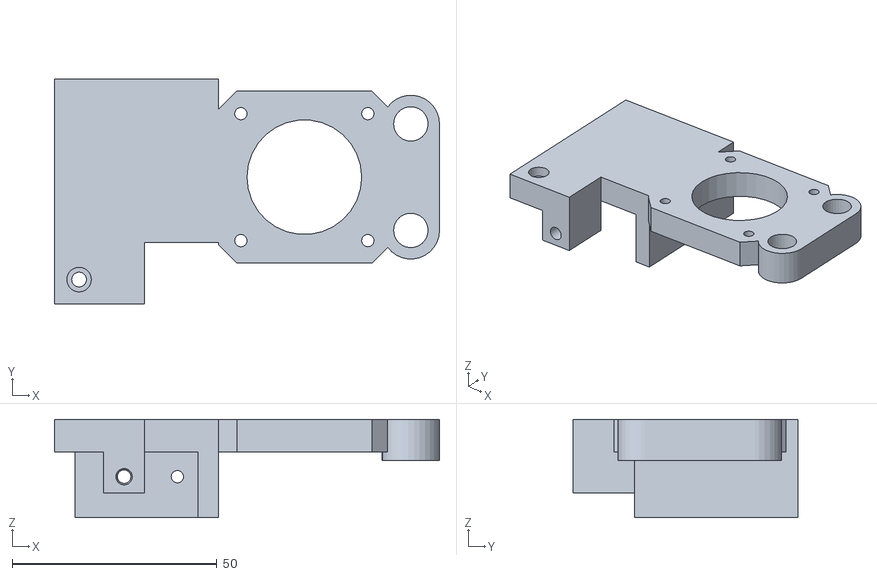
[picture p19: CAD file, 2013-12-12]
hardware/feeder/base_plate.stl
94.0 x 55.0 x 24.0

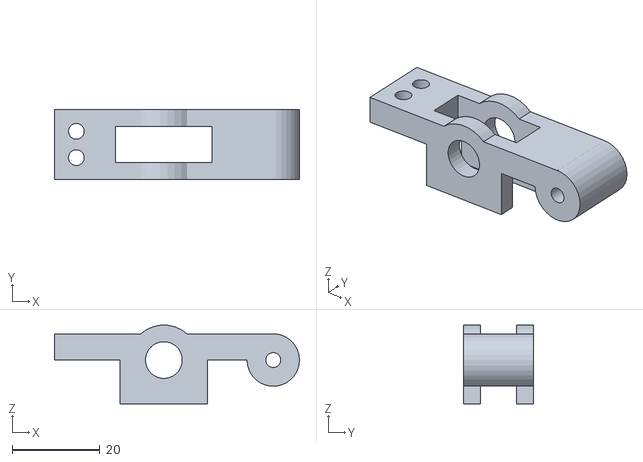
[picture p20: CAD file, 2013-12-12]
hardware/feeder/arm.stl
56.0 x 16.0 x 18.0

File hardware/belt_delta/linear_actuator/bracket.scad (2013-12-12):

$fn = 40;

module fillet(r, h) {
    translate([r / 2, r / 2, 0])

        difference() {
            cube([r + 0.01, r + 0.01, h], center = true);

            translate([r/2, r/2, 0])
                cylinder(r = r, h = h + 1, center = true);

        }
}

module axle(){
		cylinder(r=4,h=28);

}
module fillet_face(r,h,s,x){


//front
for(i = [0,1]){
translate([0,0,i*s])
rotate([0,i*90,0])
translate([0,s,s/2]) {
rotate([180,0,0])		fillet(r,s);
translate ([s,0,0]) rotate([180,180,0])		fillet(r,s);
}
}



//sides
translate([0,0,0])
for(i = [0,1]){
	translate([0,0,i*s])
	rotate([i*180,0,0])
	union(){
	rotate([90,0,0])		fillet(r,x);
	 translate([s,0,0]) rotate([90,0,180])		fillet(r,x);
	}
}

union(){
for(i = [0,1]){

rotate([0,i*180,0])
translate([-i*s,0,-i*s]){

translate([s-r,s-r,s-r]){
	difference(){
	cube([r,r,r]);
	sphere(r);
	}
}

translate([s-r,s-r,r]){
	rotate([0,90,0])
	difference(){
	cube([r,r,r]);
	sphere(r);
	}


}

}

}
	}
	
}



module bracket_bottom(){

	outer = 42;
	inner = 31/2;
	len = 0;
	plate_height = 16;
	outset = 26;

	depth=6;

color("white"){

for(i=[0,1])
mirror([i,0,0])
difference(){
union(){
	translate([10,0,0]) cube([outer,outer,5],center=true);
	//cube([outer+24,outer,5],center=true);
		translate([17,0,depth-2])cube([14,outer,10],center=true);
		translate([36,0,depth-9.6])rotate([0,60,0]){
		cube([25,outer,10],center=true);
	
	translate([-3,0,12])	
		difference(){
		cube([10,outer,20],center=true);
		for(j = [-1,1])
		rotate([0,90,0]){
		translate([-2,j*13,-10])
		cylinder(r=4,h=25);

		if(j == -1)
		translate([-10,j*outer/2,0]) rotate([0,0,0]) fillet(8,25);
		else
		translate([-10,j*outer/2,0]) rotate([180,0,0]) fillet(8,25);

		}

		}

		}

		translate([27,0,depth])rotate([90,0,0])cylinder(r=8,h=outer,center=true);




}
	translate([24,0,depth-1])cube([2,outer+2,2],center=true);
	translate([16,0,depth-2.5])cube([25,outer+2,2],center=true);
	translate([27,0,depth])rotate([90,0,0])cylinder(r=4,h=outer+2,center=true);
	for(i = [0:4])
	rotate(i*360/4)
	translate([inner,inner,0])	cylinder(r=1.7, h=30,center=true);
	cylinder(r=15, h=30,center=true);
	translate([0,0,-depth-4])cube([outer+80,outer+2,15],center=true);

}
//		for(i = [-1,1])		


}
}



module bracket_top(){

	outer = 42;
	inner = 31/2;
	len = 0;
	plate_height = 16;
	outset = 26;

	depth=6;

color("white"){
difference(){

for(i=[0,1])
mirror([i,0,0])
difference(){
union(){
	translate([10,0,0]) cube([outer,outer,5],center=true);


translate([0,0,-4]){

	translate([0,0,-2]) cylinder(r=15,h=2);
	translate([0,0,24]) cylinder(r=15,h=2);



	difference(){
		cylinder(r=15,h=26);
		cylinder(r=11.05,h=68,center=true);
	}
}
		difference(){
		translate([17,0,depth-2])cube([14,outer,10],center=true);
		translate([0,0,5.5]) cylinder(r=17, h=8,center=true);
		}
		translate([36,0,depth-9.6])rotate([0,60,0]){
		cube([25,outer,10],center=true);
	
	translate([-3,0,12])	
		difference(){
		cube([10,outer,20],center=true);
		for(j = [-1,1])
		rotate([0,90,0]){
		translate([-2,j*13,-10])
		cylinder(r=4,h=25);

		if(j == -1)
		translate([-10,j*outer/2,0]) rotate([0,0,0]) fillet(8,25);
		else
		translate([-10,j*outer/2,0]) rotate([180,0,0]) fillet(8,25);

		}

		}

		}

		translate([27,0,depth])rotate([90,0,0])cylinder(r=8,h=outer,center=true);




}
	union(){
	translate([24,0,depth-1])cube([2,outer+2,2],center=true);
	translate([16,0,depth-2.5])cube([25,outer+2,2],center=true);
	translate([27,0,depth])rotate([90,0,0])cylinder(r=4,h=outer+2,center=true);
	for(i = [0:4])
	rotate(i*360/4)
	translate([inner,inner,0])	cylinder(r=1.7, h=30,center=true);
translate([0,0,-4])	cylinder(r=11.05, h=20);
translate([0,0,-8])	cylinder(r=8, h=40);
	translate([40,0,-depth-4])cube([outer,outer+2,15],center=true);

	}

}
//		for(i = [-1,1])		



//#		translate([-14,2,2.5]) cube([28,10,13]);
	translate([0,0,2.5])
	difference(){
		cylinder(r=17,h=12);
	translate([-20,0,0])	cube(40,30,20);
//		cylinder(r=11,h=68,center=true);
	}
}}
}



//bracket_top();
//bracket_bottom();

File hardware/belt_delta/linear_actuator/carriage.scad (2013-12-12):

include <../../lib/LM8UU.scad>;
include <bracket.scad>;
include <../../hardware/extruder.scad>
$fn = 40;

carriage_clamp();

module carriage_clamp(){
color("white"){
difference(){
union(){
cube([8,12,4]);
translate([4,0,0]){
	cylinder(r=4,h=4);
	translate([0,12,0]) cylinder(r=4,h=4);
}
}

translate([4,0,-1]){
	cylinder(r=1.7,h=7);
	translate([0,12,0]) cylinder(r=1.7,h=7);
}

}}
}

module carriage(){
color("white"){

difference(){
union(){


difference(){
translate([0,10,8]) rotate([0,270,0])fillet(9,32);
for(j = [-10,3])
	translate([j,10,0])
		cube([7,10,20]);

for(j = [-22,15])
	translate([j,17,0])
		cube([7,10,20]);


}


difference(){
for(i = [0,1])
mirror([i,0,0]){
difference(){
translate([0,-10,0]) cube([41,20,24]);
translate([27,0,-1]) cylinder(r=15/2,h=26);
translate([27,-4,-1]) cube([20,8,26]);



translate([41,0,0]) rotate([270,180,0])fillet(5,25);
translate([41,0,24]) rotate([90,180,0])fillet(5,25);


}


//bearing
//translate([27,0,0]){LM8UU();}
}

translate([4,-7,-1]) cube([12,14,26]);
translate([-3,-3,-1]) cube([8,6,26]);
translate([-10,-3,-1]) cube([4,6,26]);
}
translate([0,4,0]) 
difference(){
traxxis_mount();
translate([0,-1,-1]) cube([20,5,12]);
}
}

for(j = [0,16])
for(i = [0,1])
translate([0,0,j])
mirror([i,0,0]){
translate([-37,20,4]) rotate([90,0,0]) cylinder(r=1.6,h=40);
translate([-37,13,4]) rotate([90,0,0]) cylinder(r=4,h=6);
translate([-37,-7,4]) rotate([90,0,0]) cylinder(r=4,h=6);
}

for(i = [0,1])
mirror([0,i,0]){
translate([-8,6,-1]){ rotate([0,0,0]) cylinder(r=1.7,h=30);
// hex(s=4,d=5);
cylinder(r=3.5,h=4);
}
}
//end stop pole
translate([0,13,-1]){ rotate([0,0,0]) cylinder(r=1.5,h=16);

}

}

}}


carriage();
//platform();
//translate([-12,-6,8]) carriage_clamp();

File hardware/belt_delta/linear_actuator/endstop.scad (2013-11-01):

$fn=100;

difference(){
union(){
	translate([-3,-1,0]) cube([10,2,10]);
	cylinder(r=2.5,h=5);
}

translate([0,0,-1])
cylinder(r=1.5,h=4);
}

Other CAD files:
hardware/belt_delta/linear_actuator/strut.scad
OpenSCAD/extruder.scad
OpenSCAD/plate.scad
hardware/belt_delta/assembled.scad
hardware/belt_delta/bracket_tests/bracket.scad
hardware/belt_delta/bracket_tests/bracket2.scad
hardware/feeder/feeder.scad
hardware/feeder/out_feed.scad
hardware/hardware/bracket.scad
hardware/hardware/extruder.scad
hardware/threaded_delta/assembly.scad
hardware/threaded_delta/linear_actuator/carriage.scad
hardware/threaded_delta/linear_actuator/plate.scad
hardware/threaded_delta/linear_actuator/top_coupler.scad
software/transmitter/box/box.scad

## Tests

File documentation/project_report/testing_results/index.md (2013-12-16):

Testing and Results
===================

![accuracy]
![speed]
![repeatability]

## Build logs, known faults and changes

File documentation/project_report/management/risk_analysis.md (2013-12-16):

Risk Analysis
=============

Risk mitigation is one of the most important aspects of managing a project. Possible predicted risks should be actively avoided. However not all are are forseen or are avoidable, in such case we should attempt to minimise the impact.

List of risks
-------------

| Risk (event)                     | Likelihood (H/M/L) | Impact (H/M/L) | Action |
|──────────────────────────────────|────────────────────|────────────────|────────|
|──────────────────────────────────|────────────────────|────────────────|────────|
| Development starts late          | M                  | L              |      2 |
| Schematics Incorrect             | M                  | L              |      1 |
| PCB Incorrect                    | M                  | L              |      1 |
| Unobtainable parts               | H                  | L              |      3 |
| Components break                 | H                  | M              |      3 |
| Underestimate Project time frame | M                  | H              |      2 |
| Underestimate Complexity         | H                  | H              |      4 |
| Implementation does not function | M                  | M              |      1 |
| Incomplete project threat        | L                  | H              |      4 |
| Code is lost / corrupted         | L                  | L              |      5 |
| Hardware issues                  | L                  | M              |      1 |
|──────────────────────────────────|────────────────────|────────────────|────────|
			List of possible risks

List of actions
---------------

| Action | Comment                                                                                                         |
|────────|─────────────────────────────────────────────────────────────────────────────────────────────────────────────────|
|────────|─────────────────────────────────────────────────────────────────────────────────────────────────────────────────|
|      1 | Diagnose and debug, attempt to develop work around depending on project stage. Redesign if problem is critical. |
|      2 | Adjust Gantt chart, design new tactics and re-prioritise if required.                                           |
|      3 | Obtain new components. If unavailable or time frame does not permit, attempt to use alternative.                |
|      4 | Discontinue development on selected components. Adopt complete and tested consumer alternatives.                |
|      5 | Pull latest commit from off site Git repository server. Backups should be made nightly.                         |
|────────|─────────────────────────────────────────────────────────────────────────────────────────────────────────────────|
				List of actions

Mitigated Risks
---------------

During the project a few events were mitigated with their associated actions. The following paragraphs discuss what occurred and how it was handled.

 *Schematics Incorrect* The first revision had many issues. All were able to be averted during the prototyping stage by making modifications to the PCB. All current issues were amended on the revision 2 board.

 *Components break* 4 Stepper drivers were damaged due to a poor PCB design. The new revision fixed these issues.

 *Underestimate Project time frame* Deadlines were met by shifting priorities around. An extension was later required for the project report.

 *Incomplete Project threat* Continued project development after final university deliverables have been met.

 *Hardware issues* Design kept improving and complete reworks were undertaken.

 *Code is corrupted* The current fork of code was in a non functioning state for the final presentation. Using Git as version control, I was able to checkout a previous working state ready for the presentation.

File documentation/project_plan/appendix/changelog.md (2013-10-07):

Change Log
==========

8/4/2013 - Initial Version
27/9/2013 - Converted to markdown

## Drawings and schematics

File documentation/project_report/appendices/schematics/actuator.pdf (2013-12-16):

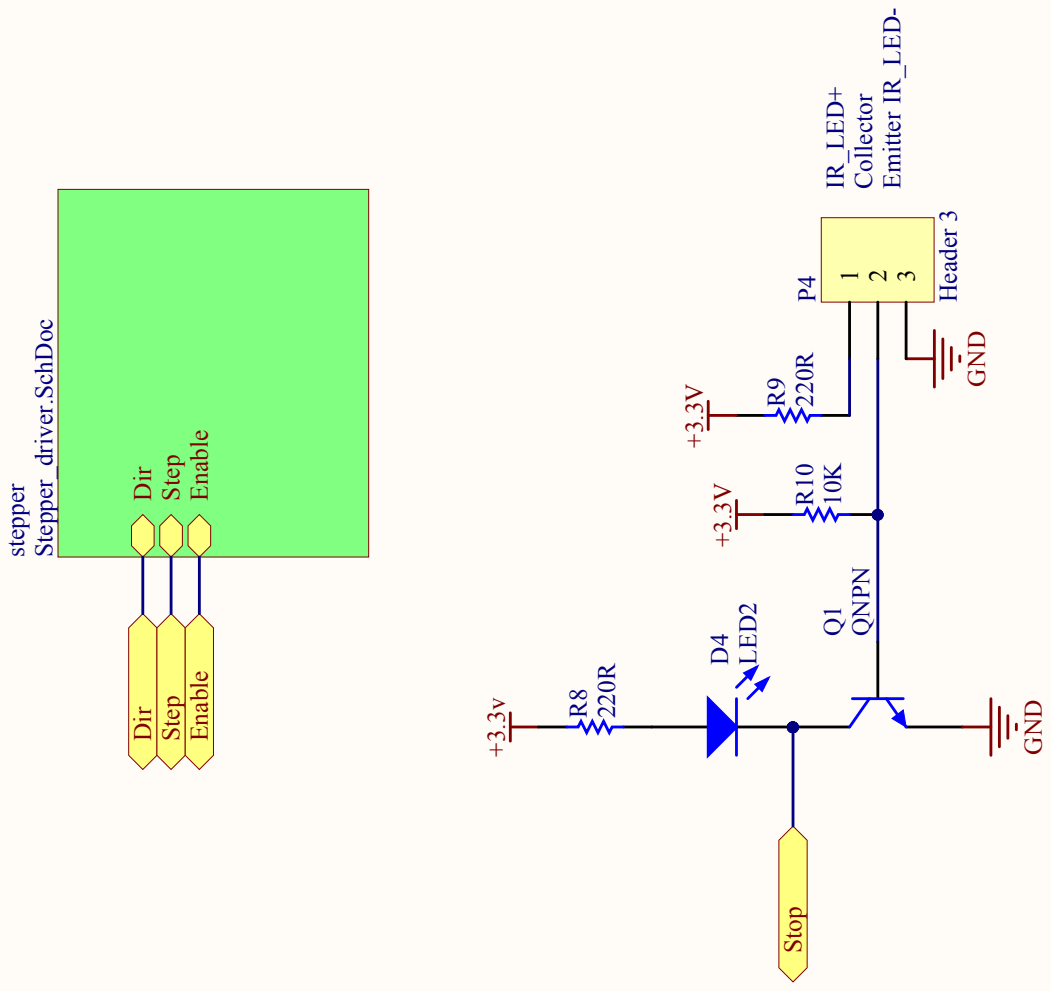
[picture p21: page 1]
Title; Dir; Step; Enable; stepper; Stepper_driver.SchDoc; Stop; GND; IR_LED+; IR_LED-; Collector; Emitter; Header 3; QNPN; LED2

Number Revision Size

File: E:\Documents\..\Linear_actuator.SchDoc Drawn By:

Date: 12/16/2013 Sheet of

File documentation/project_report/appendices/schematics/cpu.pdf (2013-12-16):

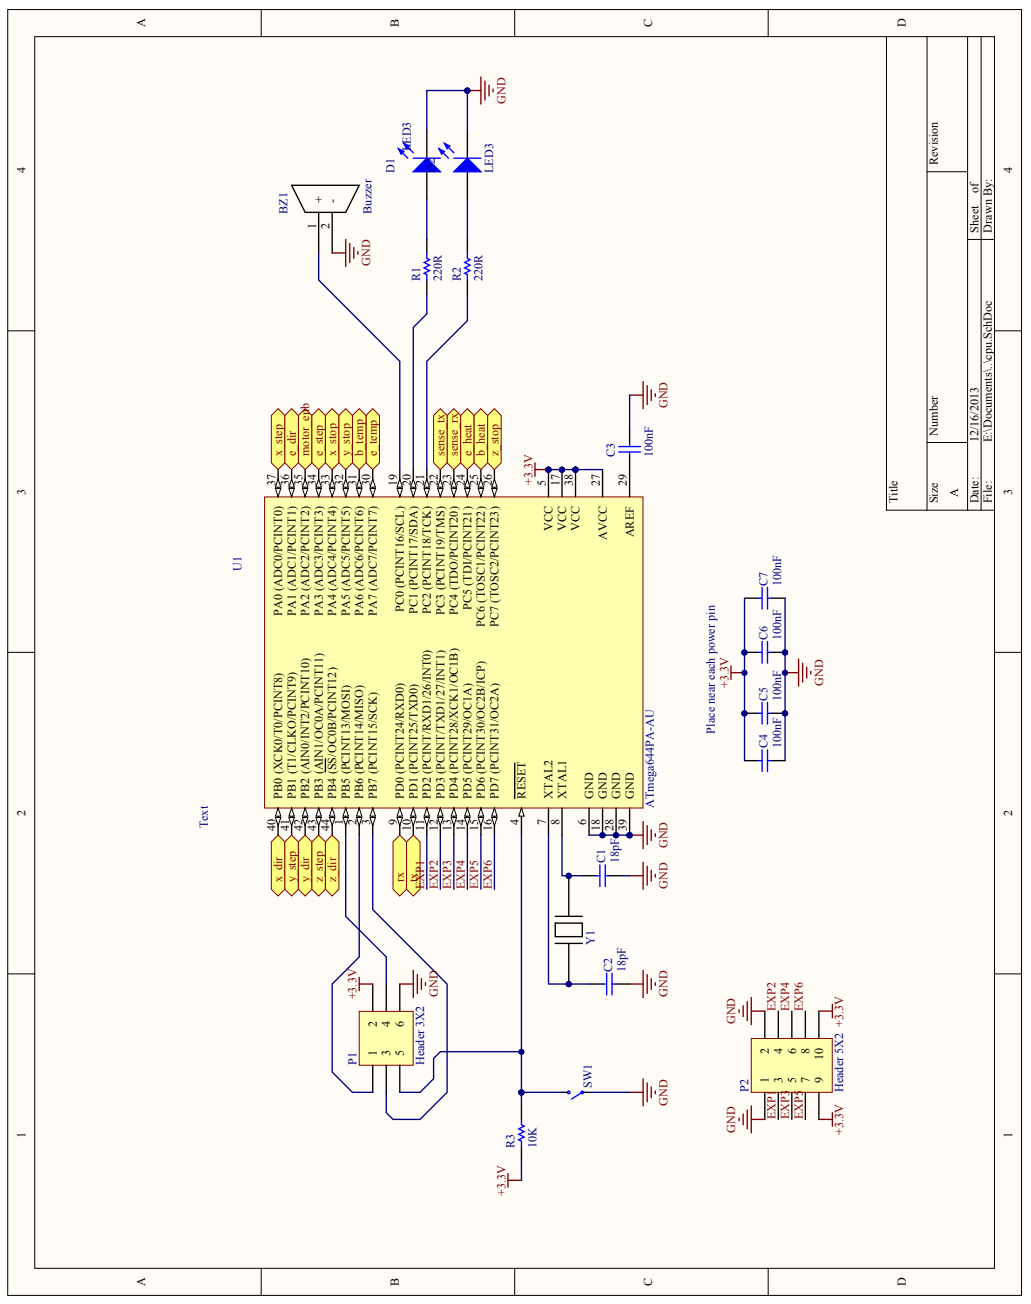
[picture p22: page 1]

File: E:\Documents\..\cpu.SchDoc Drawn By:

Place near each power pin

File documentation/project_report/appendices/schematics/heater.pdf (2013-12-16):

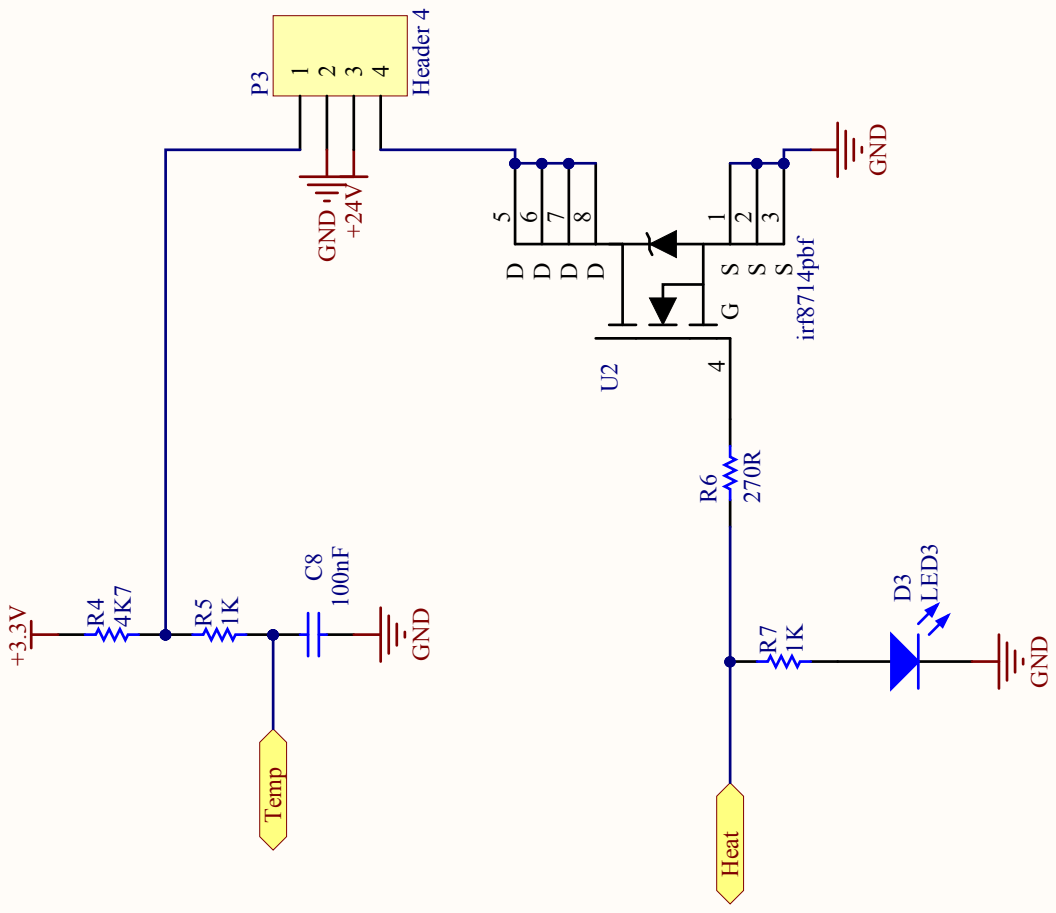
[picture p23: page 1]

File: E:\Documents\..\heater.SchDoc Drawn By:

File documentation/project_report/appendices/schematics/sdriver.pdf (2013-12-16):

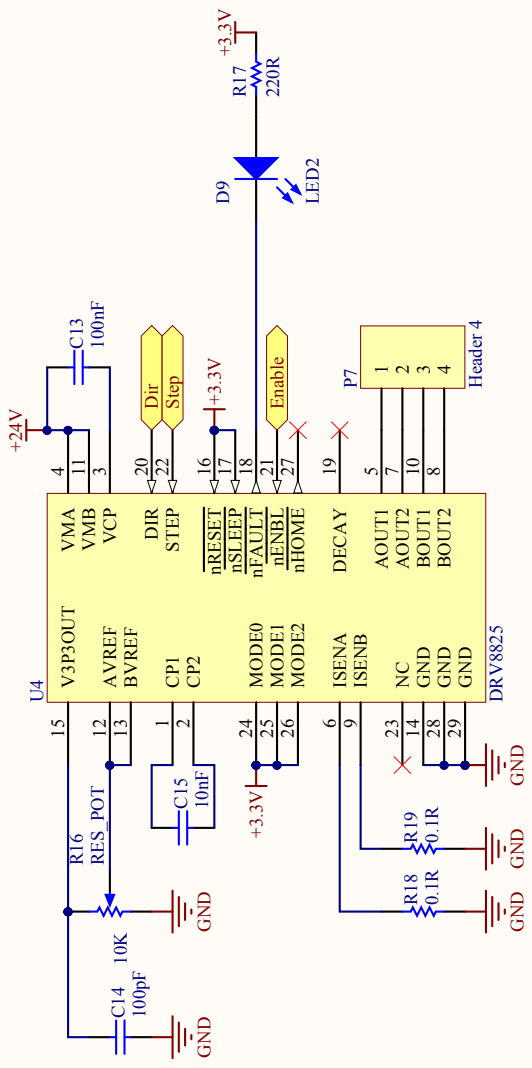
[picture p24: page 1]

File: E:\Documents\..\Stepper_driver.SchDoc Drawn By:

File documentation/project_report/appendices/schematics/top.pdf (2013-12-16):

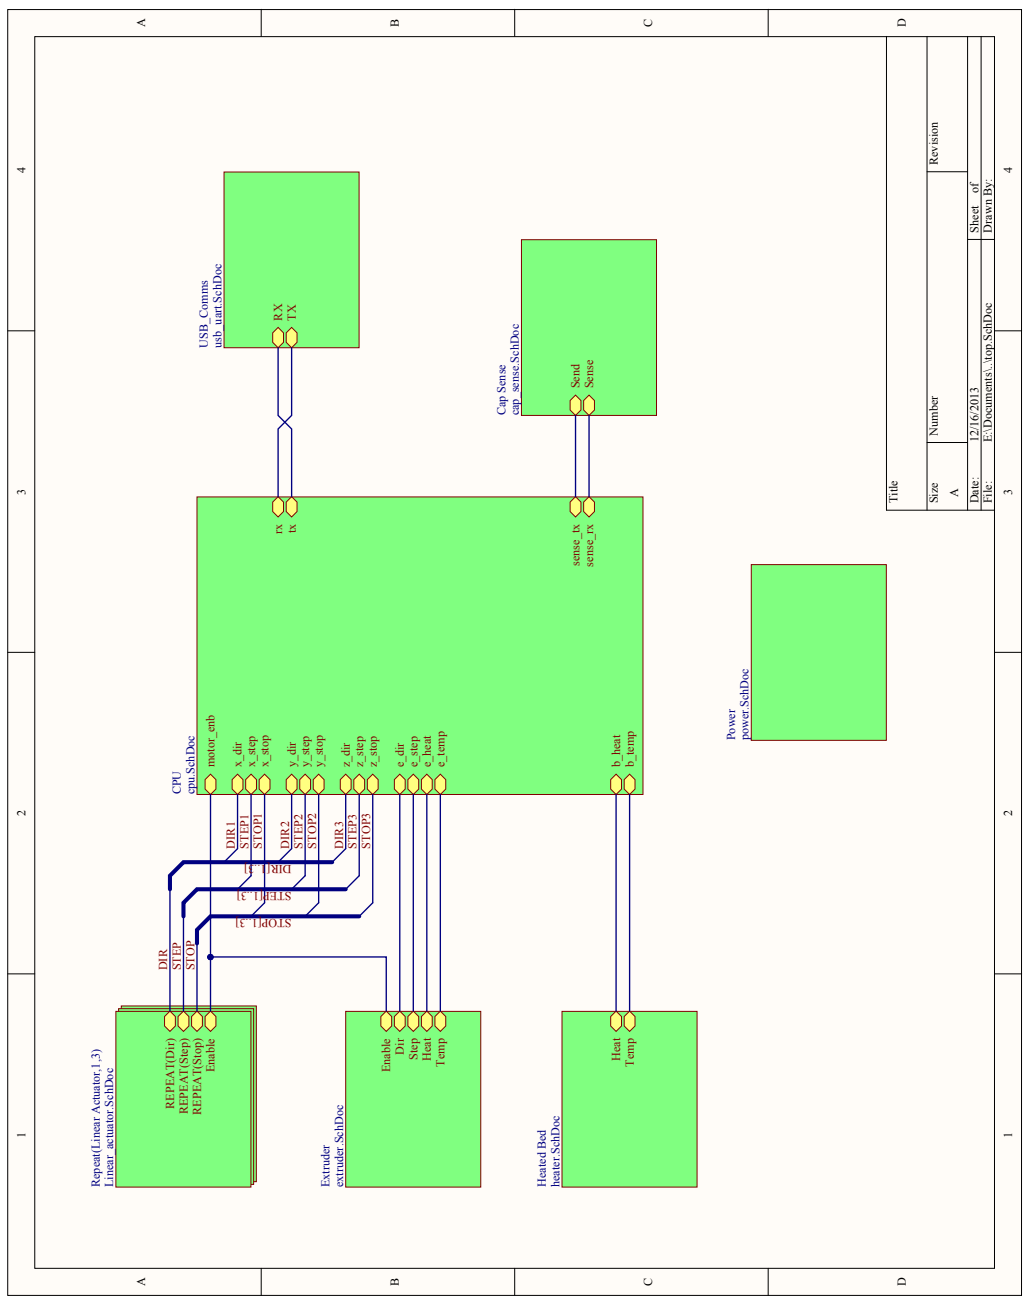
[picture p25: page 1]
Title; x_step; motor_enb; x_dir; y_step; y_dir; z_step; z_dir; e_step; e_dir; e_heat; e_temp; b_heat; b_temp; top; y_stop; z_stop; sense_rx; sense_tx; CPU; cpu.SchDoc; REPEAT(Dir); REPEAT(Step); Enable; REPEAT(Stop); Linear_actuator.SchDoc; Temp; Heat; Heated Bed; heater.SchDoc; Dir; Step; Extruder; extruder.SchDoc; Power; power.SchDoc; USB_Comms; usb_uart.SchDoc; STOP3; STEP3; DIR3; STOP2; STEP2; DIR2; STOP1; STEP1; DIR1; DIR; STEP; STOP; Sense; Send; Cap Sense; cap_sense.SchDoc; NLDIR010030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

Number Revision Size

File: E:\Documents\..\top.SchDoc Drawn By:

Date: 12/16/2013 Sheet of

Repeat(Linear Actuator,1,3)

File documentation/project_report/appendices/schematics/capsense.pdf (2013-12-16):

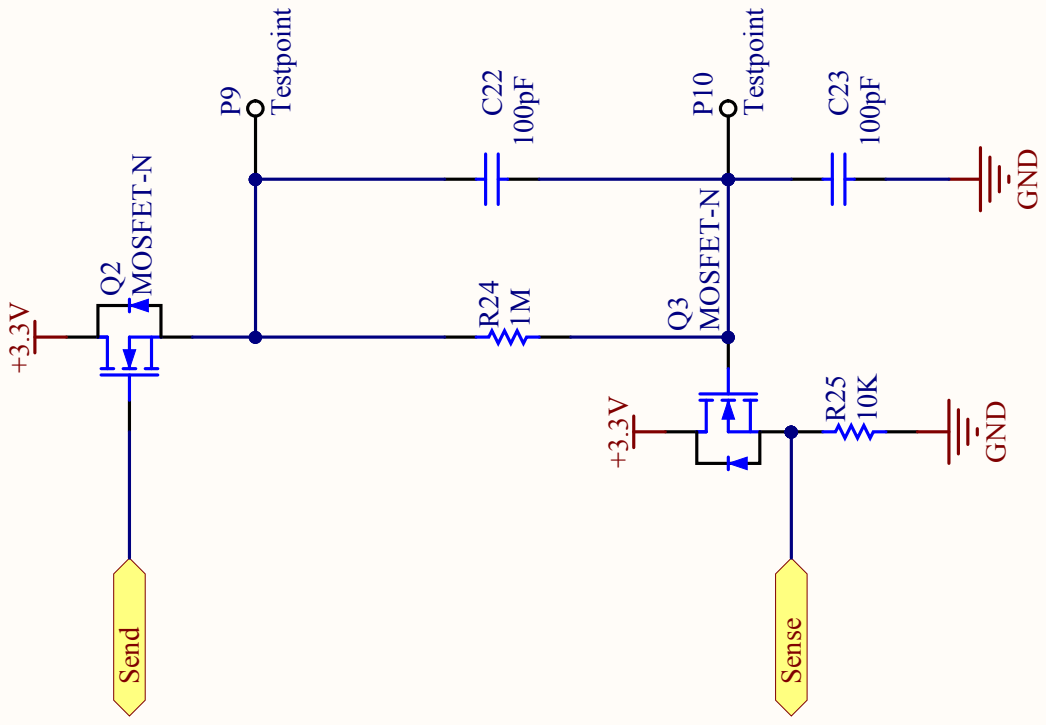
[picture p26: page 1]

File: E:\Documents\..\cap_sense.SchDoc Drawn By:

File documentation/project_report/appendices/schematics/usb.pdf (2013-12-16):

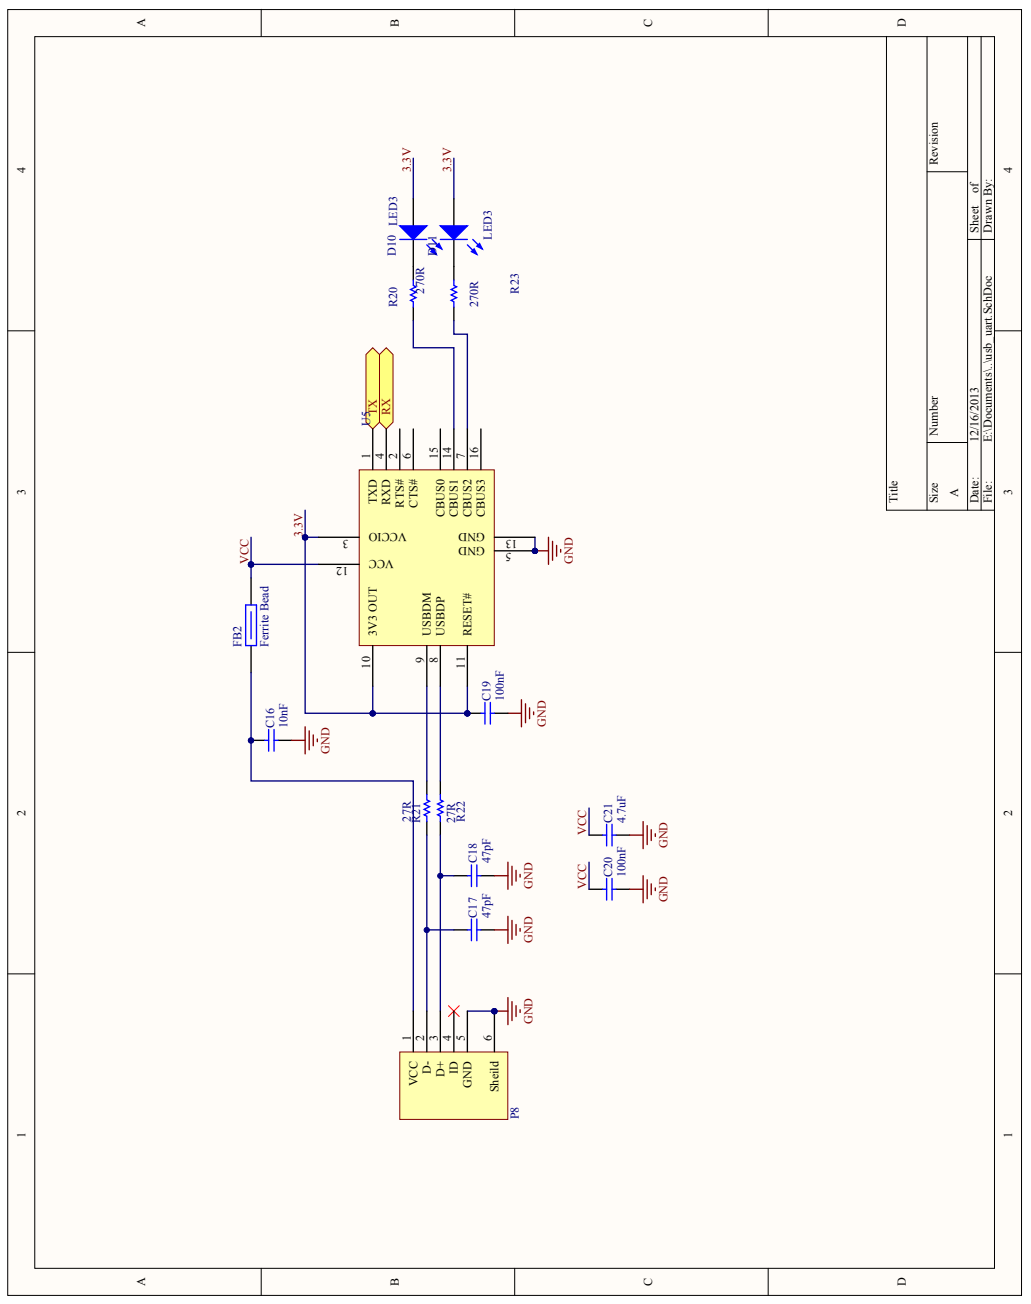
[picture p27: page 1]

File: E:\Documents\..\usb_uart.SchDoc Drawn By:

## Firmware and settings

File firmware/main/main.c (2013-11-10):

#include "etc/byte.h"
#include "etc/config.h"
#include "sys/port.h"
#include "dev/stepper/stepper.h"
#include <util/delay.h>
#include "lib/position/position.h"


int main(void){
pin_config_out(r_led);

Stepper *stepper_x = stepper_init(x_step,x_dir,motor_enb);
Stepper *stepper_y = stepper_init(y_step,y_dir,motor_enb);
Stepper *stepper_z = stepper_init(z_step,z_dir,motor_enb);
//Stepper *stepper_e = stepper_init(e_step,e_dir,motor_enb);

stepper_dir(stepper_x,1);
stepper_dir(stepper_y,1);
stepper_dir(stepper_z,1);


a1_step = 180;
a2_step = 180;
a3_step = 180;
//distance = 18000*20;
stepper_start_frame();

	while(1);
}

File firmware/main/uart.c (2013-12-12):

#include "etc/byte.h"
#include "etc/config.h"
#include "dev/stepper/stepper.h"
#include "lib/position/position.h"
#include "sys/port.h"
#include "sys/console.h"
#include "dev/uart/uart.h"
//#include "dev/thermistor/thermistor.h"

#include <util/delay.h>
#include <avr/interrupt.h> 


int main(void){

	pin_config_out(g_led);
	pin_config_out(r_led);
	pin_config_out(e_heat);
	pin_config_out(b_heat);
	pin_config_out(buzzer);

	pin_config_in(x_stop);
	pin_config_in(y_stop);
	pin_config_in(z_stop);
	pin_config_in(sense_rx);

	pin_high(e_heat);
	pin_high(b_heat);

	stepper_init(x_step,x_dir,motor_enb);
	stepper_init(y_step,y_dir,motor_enb);
	stepper_init(z_step,z_dir,motor_enb);
	stepper_start_frame();
	steppers_disable();


	uart_init();
	console_init();
//	thermistor_init();
	console_prompt();
}

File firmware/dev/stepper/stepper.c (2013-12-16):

#include "stepper.h"

volatile Stepper* steppers[4];
volatile int speed = 4000;
volatile int speed_min = 4000;//I want to be able to notice it slow down for tests
volatile int speed_max = 1;
volatile int speed_accel = 10;
volatile int speed_jerk = 100;
volatile int speed_jerk_count = 0;

volatile unsigned int steps = 0;
volatile int s = 0;
volatile char stepper_active = 0;


//prototypes
void accel(long double change);

Stepper *stepper_init(Pin *step, Pin *direction, Pin *enable){
	Stepper *stepper = (Stepper * ) malloc( sizeof( Stepper ) );
	stepper->step = step;
	stepper->direction = direction;
	stepper->enable = enable;

	pin_low(step);
	pin_high(direction);
	pin_low(enable);

	pin_config_out(step);
	pin_config_out(direction);
	pin_config_out(enable);

	steppers[s] = stepper;
	s++;

	return stepper;
}


void stepper_start_frame(){
	cli();
	TCCR1A = 0;     // set entire TCCR1A register to 0
	TCCR1B = 0;     // same for TCCR1B

	OCR1A = speed;
    // turn on CTC mode:
	TCCR1B |= (1 << WGM12);
    // Set CS10 and CS12 bits for 1024 prescaler:
 //   TCCR1B |= (1 << CS00);
   // TCCR1B |= (1 << CS12);
    // enable timer compare interrupt:
   // TIMSK1 |= (1 << OCIE1A);



//	TCCR1B |= (1 << WGM12); // Configure timer 1 for CTC mode 
//	TIMSK1 |= (1 << OCIE1A); // Enable CTC interrupt 
//	OCR1A   = speed; // Set CTC compare value to 1Hz at 1MHz AVR clock, with a prescaler of 64 
//	TCCR1B |= ((1 << CS10)) | (1 << CS11); // Start timer at Fcpu/64 
//	TCCR1B |= ((1 << CS00)); // Start timer at Fcpu/64 

	sei(); //  Enable global interrupts 


}

void stepper_step(Stepper *stepper){
	pin_high(stepper->step);
	pin_low(stepper->step);

}


void stepper_dir(Stepper *stepper,int dir){
	pin_set(stepper->direction,dir);
}


void set_speed( int s){
	speed = s;
	OCR1A = speed; // Set CTC compare value to 1Hz at 1MHz AVR clock, with a prescaler of 64 
}


int get_speed(){
	return speed;
}

void accel(long double change){

speed_jerk_count++;
if(speed_jerk_count > speed_jerk){
speed_jerk_count = 0;
printf("s:%i\n",speed);


	if(change < 20	){
		if(speed < speed_min)
			speed += speed_accel;
	}else{ 
		if(speed > speed_max)
			speed -= speed_accel;
	}

	OCR1A = speed; 

}
}


void steppers_enable(){
	cli();
	pin_low(steppers[0]->enable);
	pin_high(r_led);
	TCCR1B |= ((1 << CS12)); // Start timer at Fcpu/64 
//	TCCR1B |= ((1 << CS10) ); // Start timer at Fcpu/64 
	TIMSK1 |= (1 << OCIE1A); // Enable CTC interrupt 
	set_speed(speed_min);
	stepper_active = 1;
	sei(); //  Enable global interrupts 
//	printf("enb\n");
}

void steppers_disable(){
	cli();
	pin_high(steppers[0]->enable);
	pin_low(r_led);
	TCCR1B &= ~( (1 << CS12)); // Start timer at Fcpu/64 
//	TCCR1B &= ~((1 << CS10)); // Start timer at Fcpu/64 
	TIMSK1 &= ~(1 << OCIE1A); // Enable CTC interrupt 
	set_speed(speed_min);
	stepper_active = 0;
	sei(); //  Enable global interrupts 
//	printf("dis\n");
}



int i = 0;

ISR(TIMER1_COMPA_vect) { 
	if( motion_current->distance > 0 || hold_on == 1 ){

		if( (int)(a1_cycle + motion_current->motor[0].step) != (int)(a1_cycle)   ){
			pin_toggle(steppers[0]->step);
		}

		if( (int)(a2_cycle + motion_current->motor[1].step) != (int)(a2_cycle)   ){
			pin_toggle(steppers[1]->step);
		}

		if( (int)(a3_cycle + motion_current->motor[2].step) != (int)(a3_cycle)   ){
			pin_toggle(steppers[2]->step);
		}

			a1_cycle += motion_current->motor[0].step;
			a2_cycle += motion_current->motor[1].step;
			a3_cycle += motion_current->motor[2].step;

			motion_current->distance--;
			motion_current->distance_change--;

			accel(motion_current->distance_change);


	}else
	shift_motion();

}

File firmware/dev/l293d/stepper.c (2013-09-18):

#include "stepper.h"

const static byte map[] = {
	b0|b1,
	b1|b2,
	b2|b3,
	b0|b3
};

void step(Stepper *stepper, int i );

Stepper *stepper_init(Port *port){
	Stepper *stepper = (Stepper * ) malloc( sizeof( Stepper ) );
	stepper->port = port;
	stepper->dir = 0;

	port_config_out(port);
	port_low(port);

	return stepper;
}

void stepper_step(Stepper *stepper){

	if(stepper->dir == 0)
	for(int i = 0; i < 4; i++){
		step(stepper,i);
	}	
	else
	for(int i = 3; i >= 0; i--){
		step(stepper,i);
	}	

}


void step(Stepper *stepper,int i ){
	port_set(stepper->port, map[i]);
		__delay_cycles (4000);
}

void stepper_dir(Stepper *stepper,int dir){
	stepper->dir = dir;
}

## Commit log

2013-07-25 Initial linear actuator tests
    [LM8UU.scad, assembly.scad, carriage.scad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]
2013-07-26 Started platform test and updated carriage
    [LM8UU.scad, assembly.scad, carriage.scad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]
2013-07-26 renamed folder
    [LM8UU.scad, assembly.scad, carriage.scad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]
2013-07-27 organised folder structure
    [assembly.scad, bracket.scad, carriage.scad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]
2013-07-27 Preped for next test; fixed threaded coupler and carriage
    [carriage.scad, plate.scad, top_coupler.scad]
2013-07-30 Fixed up lengths of platform arms, hex sizes, linear bearing coupler sizes
    [carriage.scad, extruder.scad]
2013-09-05 tweaks to frame
2013-09-18 small deltabot 3 init
    [assembled.scad, assembly.scad, bracket.scad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]
2013-09-18 added stubbed out code and renmaed folders
    [assembled.scad, assembly.scad, bracket.scad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]
2013-09-24 larger strut holders
    [assembled.scad, bracket.scad, carriage.scad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]
2013-10-07 init rev2
    [Linear_actuator.SchDoc, Stepper_driver.SchDoc, cap_sense.SchDoc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]
2013-10-07 various small fixes
    [strut.scad]
2013-10-08 partial uart and console
2013-10-13 added spi, lcd, uart, thermistor
    [bracket.scad, carriage.scad, extruder.scad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]
2013-10-27 some movement and toggle fixes
    [bracket.scad]
2013-11-01 added endstop interrupter
    [endstop.scad]
2013-11-27 queue and timer motion
2013-11-29 stubbed out transmitter software
    [box.scad, box.stl]
2013-12-12 large backup
    [arm.stl, assembled.scad, base_plate.stl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]
2013-12-16 transmitter fixes
    [box.scad, box.stl]
